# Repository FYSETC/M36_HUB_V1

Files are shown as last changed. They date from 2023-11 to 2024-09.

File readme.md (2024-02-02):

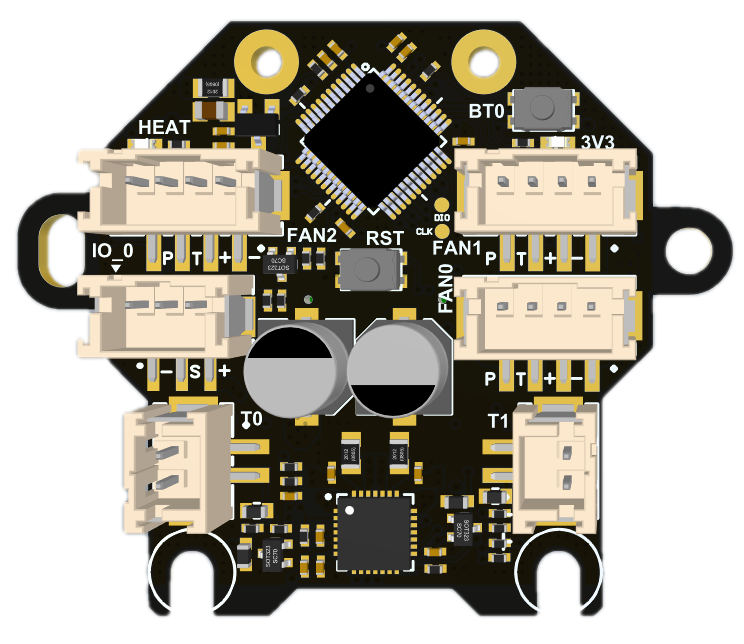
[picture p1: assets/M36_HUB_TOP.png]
M36_HUB_TOP


## 1. Introduction

M36集线板是专门为使用36圆形步进电机（Nema14）而设计的，可以用在mini Stealthburner 或者其他使用36电机的打印头上。该板可以配合多种主板使用，尤其是我们的catalyst和BullAnt。配合专用连接线材也可适配任何其他使用klipper的系统。

M36分为两个版本，主要是电机驱动芯片不一样，普通版本为TMC2209，与Catalyst主板配合使用；Lite版本为GC6609，与BullAnt主板配合使用。

The M36 hub board is specially designed for use with 36 circular stepper motors (Nema14) and can be used on mini Stealthburner or other print heads using 36 motors. This board can be used with a variety of motherboards, especially our catalyst and BullAnt. With special connection cables, it can also be adapted to any other system using klipper.

M36 is divided into two versions, mainly because of the difference in motor driver chips. The normal version is TMC2209, used with Catalyst motherboard; the Lite version is GC6609, used with BullAnt motherboard.

### 1.1 Feature

- Based on STM32F072
- USB interface or CAN（need addon board）
- Onboard TMC2209 / GC6609 (Lite Version)
- 3 x 4Pin(2pin/3pin compatible) controlled Fans (default VIN power supply, 5V optional)
- 1x signal input / output interface (default 5V power supply, VIN optional , with level shift)
- 2x signal input and output interface (3.3V power supply, with 10K pull-up resistor,without level shift)
- 2X 5V single wire RGB interface (1A MAX)
- 1x 3A MAX PWM output for heating rod
- 2x ADC interface for heating temperature or other needs
- 1x onboard thermistor for board temperature or champer temperature monitor
- Comes with 250mm 4-core cable
- 24V/7A max Power Supply
- Comes with terminal housing and wire crimping tabs
- Onboard ADXL345

## 2. Hardware Guide

### 2.1 Install

5. 

### 2.2 Connectors

| Connector name | Type | Details |
| --- | --- | --- |
| IO_0 | PH2.0-3P | PB5，for input and output, with level shift,  hardware pull-up 10k resistor to 3.3v with 100R series resistor. <br><br/>Use For:  <br>Proximity switch (need 24V )<br/>mechanical switch<br/>Photoelectric switch<br/>24V 4pin fan (TCAH pin is suspended) |
| IO_12 | SH1.0-6P | 1=PB6，2=PB7, for input and output, hardware pull-up 10k resistor to 3.3v with 100R series resistor. <br><br/>Use For:  <br/>mechanical switch<br/>Photoelectric switch<br/>Any digital ouput |
| MOTOR | PH2.0-4P | TMC2209 / GC6609<br>EN : PB1<br>DIR : PB14<br>STEP : PB15<br>DIAG : PA8<br>UART : PA9 |
| INPUT | 0.5mm 2x16 BTB connector | Max 24v 7A input, CAN_TX/USBPM=PA12, CAN_RX/USBDM=PA11 |
| T0 | PH2.0-2P | PA0，ADC，4.7K pull-up to 3.3V |
| T1 | PH2.0-2P | PA3，ADC，4.7K pull-up to 3.3V |
| TB | no connector | PA2，ADC，4.7K pull-up to 3.3V, onboard 100K /3950 thermistor |
| HEAT | XH2.54-2P | PA8，MAX 3A，PWM output，max power recommended: 24V/70W |
| FAN0 | PH2.0-2P | Enable: PB11, (4pin fan = enable, 2pin/3pin fan = PWM control pin)<br/>TACH: PB12, <br/>PWM: PB10, (only for 4pin fan)<br/>0.5A MAX PWM，for fan control (default VIN，5V selectable) |
| FAN1 | PH2.0-4P | Enable: PB4, (4pin fan = enable, 2pin/3pin fan = PWM control pin)<br/>TACH: PB3, <br/>PWM: PA15, (only for 4pin fan)<br/>0.5A MAX PWM，for fan control (default VIN，5V selectable) |
| FAN2 | PH2.0-4P | Enable: PB9, (4pin fan = enable, 2pin/3pin fan = PWM control pin)<br/>TACH: PA10, <br/>PWM: PB8, (only for 4pin fan)<br/>0.5A MAX PWM，for fan control (default VIN，5V selectable) |
| RGB1 | SH1.0-3P | PB13，1A MAX sigal line RGB port, 5V，for NeoPixel, WS2812 |
| RGB2 | SH1.0-3P | PB0, 1A MAX sigal line RGB port, 5V，for NeoPixel, WS2812<br/>安装R39=0-100R，可以将RGB1和RGB2串联起来，仅用PB13控制。<br/>Install R39=0-100R, you can connect RGB1 and RGB2 in series and only use PB13 to control them. |

### 2.3 Wiring

2.3.1 With Bullant

2.3.2 With Catalyst V1

2.3.3  With Catalyst V2

2.3.4 With Spider and Raspberry Pi

### 2.4 SCH DXF STEP

Get SCH, DXF, STEP files on github:

## 3. Firmware Guide

This is only Klipper firmware support. If you are Klipper beginner please check the Klipper firmware build here:  [Installation - Klipper documentation](https://www.klipper3d.org/Installation.html#installation)

### 3.1 Firmware Update

1. Turn on the power of the machine and wait for CM68 to start completely, which will take approximately 30-90s.

2. Press and hold the BT0 button on the M6 without releasing it. Press and hold the RST button for more than 2 seconds and release it. Wait for 3 seconds and release the BT0 button;

3. Enter "lsusb" in the SSH interface and you should see the DFU device appear;

4. "cd klipper" enters the klipper directory

5. "make menuconfig" configure the firmware, as shown below:

  M36_menuconfig

6. "make flash FLASH_DEVICE=0483:df11" to compile and upload;

7. When you see the word "successfully", it means the programming is successful.

1. 打开机器电源，等待CM68完全启动，大致需要30-90s。
2. 按住M6上的BT0按钮不松开，按住RST按键2秒以上松开，等待3S，松开BT0按钮；
3. 在SSH界面输入 ‘lsusb‘ 你应该能看到 DFU 设备出现；
4. ‘cd klipper ’进入klipper目录
5. ‘make menuconfig’ 进行固件配置，如下图：
6. make flash FLASH_DEVICE=0483:df11 进行编译并烧录；
7. 当看到successfully字样的时候表示烧录成功。

### 3.2 Config

 We put the Klipper configuration file in github,  you need to get the DEVICE ID by "ls /dev/serial/by-id", then replace the id in the config file.

On Catalyst and Bull Ant motherboards, the USB path is used by default for connection, and an ID is no longer required. In theory, it can be used after updating the firmware and restarting.

我们将Klipper的配置文件放在github中，需要通过“ls /dev/serial/by-id”获取DEVICE ID，然后替换配置文件中的id。

在催化剂和公牛蚁主板上，默认使用USB路径来进行连接，不再需要ID。理论上，更新完固件，重启之后既可使用。

## Buy

[Taobao](https://item.taobao.com/item.htm?spm=a1z10.3-c.w4002-23828897339.22.229c1613tHAtLW&id=690431280049)

[Aliexpress](https://www.aliexpress.com/item/1005004880078163.html)

[Official website](https://www.fysetc.com/products/fysetc-sb-can-tool-board-based-on-stm32f072-support-klipper-with-tmc2209-axl345-acceleration-sensor-for-3d-printer-parts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)

## Contacts

QQ: 1041794121

Facebook grounp：https://www.facebook.com/groups/197476557529090

Discord：https://discord.gg/Fb6FdND4

email：support@fysetc.com

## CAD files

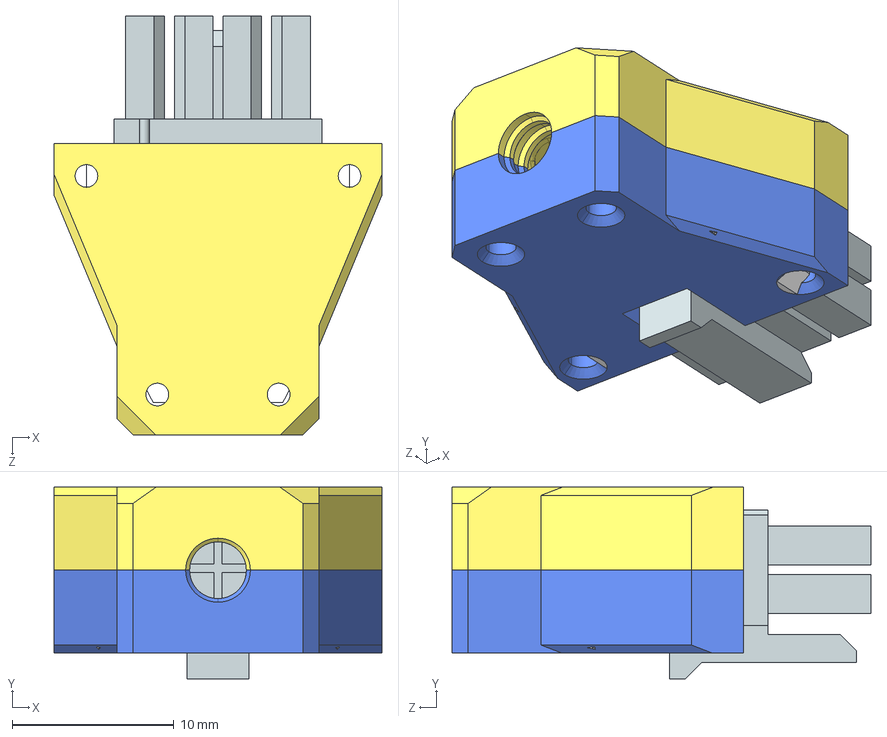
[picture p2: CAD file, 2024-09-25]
hardware/MX3.0-8P-CASE.STEP
20.3 x 11.8 x 25.9 mm
430250810_默认
Part2_默认
Part3_默认
Part4_默认

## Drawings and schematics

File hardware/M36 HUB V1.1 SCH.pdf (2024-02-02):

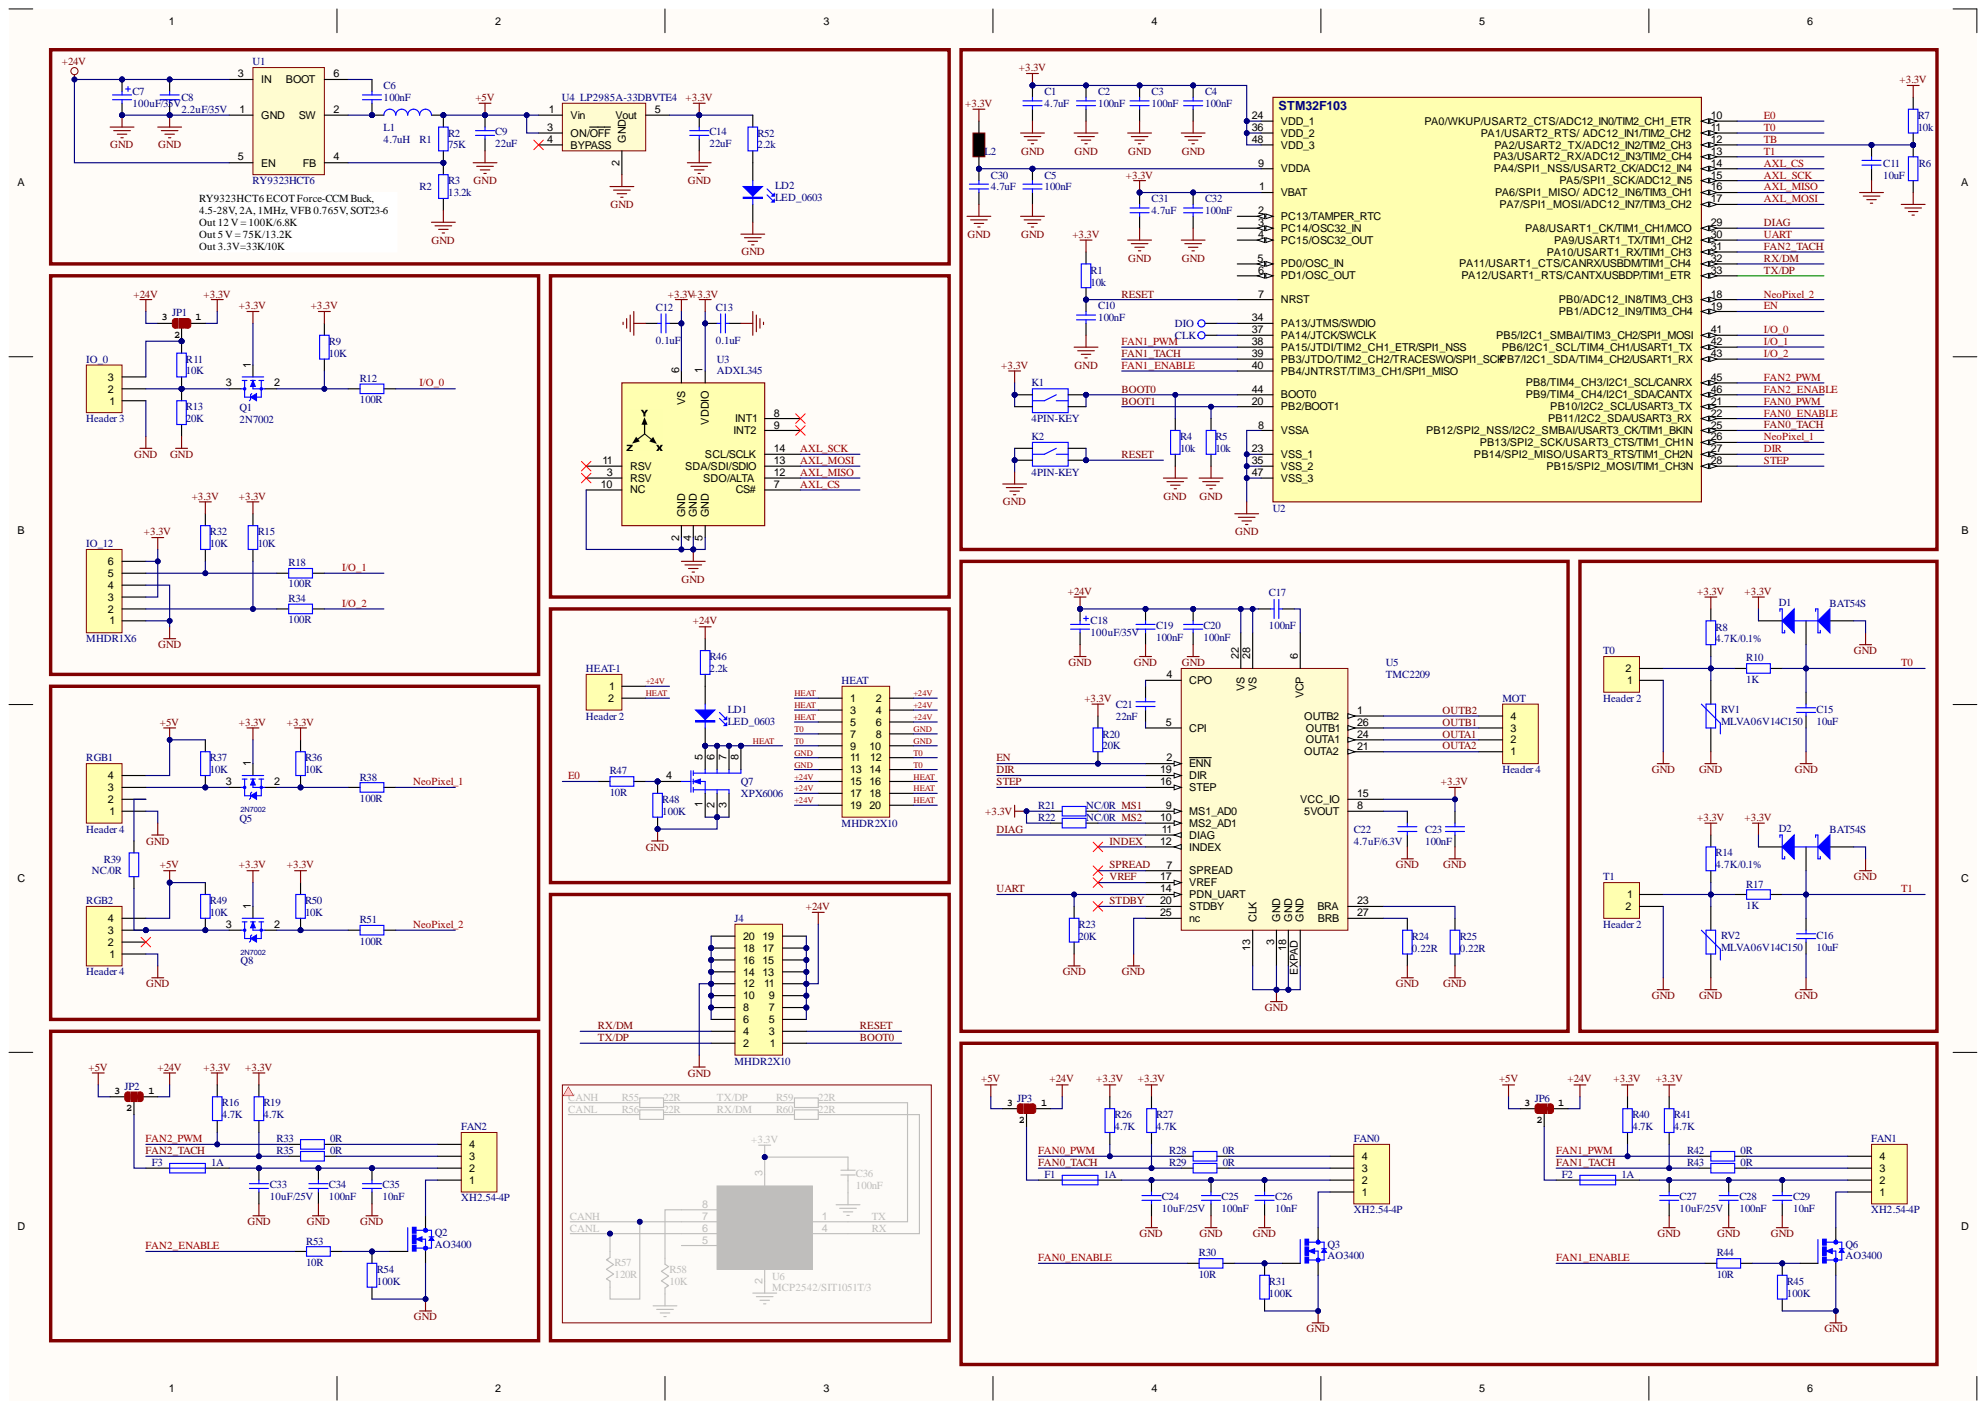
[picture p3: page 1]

C8 | GND 1

ON/OFF 3

VDD_2 36 | T0

VDDA 9 | T1

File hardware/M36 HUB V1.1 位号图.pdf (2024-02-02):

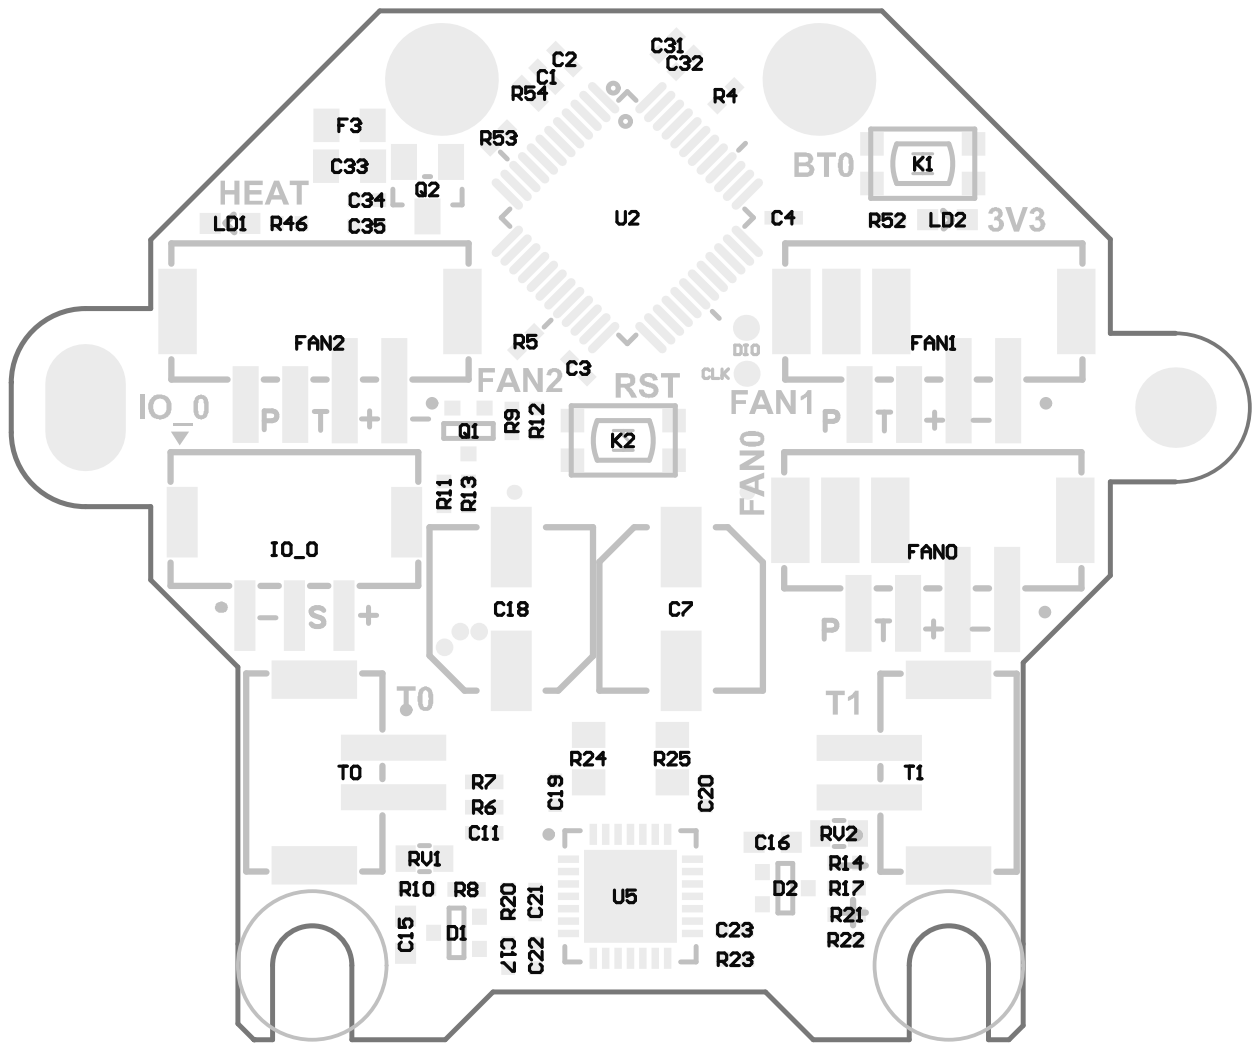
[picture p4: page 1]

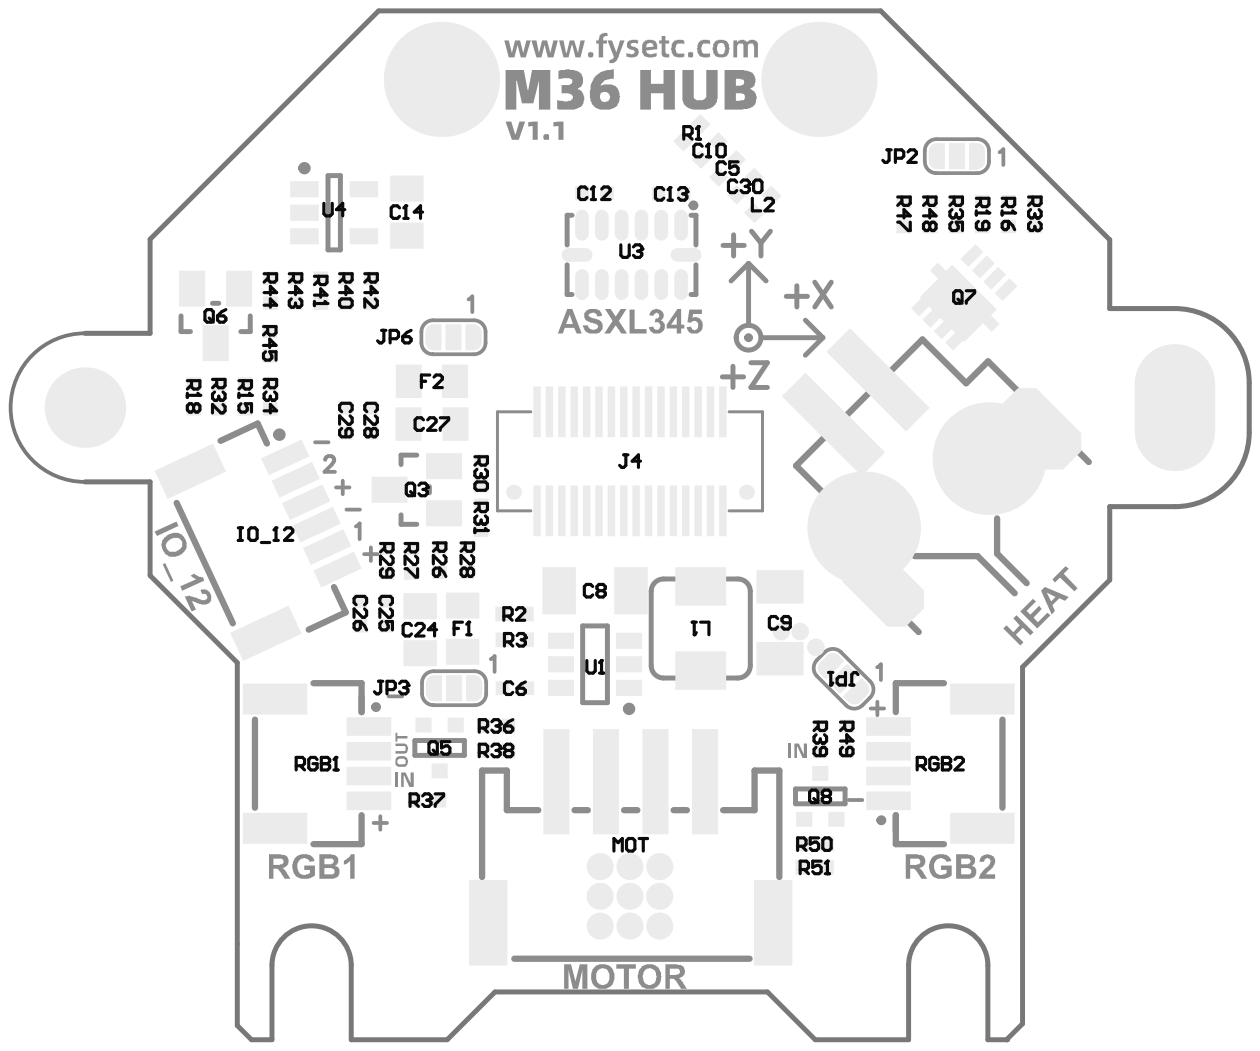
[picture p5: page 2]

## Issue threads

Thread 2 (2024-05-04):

Need Klipper config for this

zachdev, 2024-05-04:
Where is the klipper head.cfg that is required for this?

danyial, 2024-05-13:
Need it too

cdiesch, 2024-06-03:
I also need the head.cfg. My machine shipped with a dead cm68 and the replacement one does not have the correct config files.

mayder, 2024-06-19:
Need it too, because I want configure the ADXL345

kkobold, 2024-07-16:
need it too

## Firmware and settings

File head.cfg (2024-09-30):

## M36 HUB V1.1 Lite （with GC6609）
## For more info 
## https://github.com/FYSETC/M36_HUB_V1
## https://wiki.fysetc.com/M36_HUB_V1/

# This file contains common pin mappings for the Fysetc M36 HUB V1.1
# To use this config, the firmware should be compiled for the
# STM32F072 with "No bootloader" ,"Internal clock" and Communication interface USB

# How to get in DFU mode:
# 1. hold BT0 button for 2 seconds
# 2. Hold RST button for 2 seconds
# 3. Release the BT0 button
# 4. wait 2seconds
# 5. Release the RST button
# "lsusb" check if get in DFU mode

# After running "make", run the following command to flash the board:
# "dfu-util -R -a 0 -s 0x08000000:leave -D out/klipper.bin" to upload
# or "make flash FLASH_DEVICE=0483:df11" compile and upload at once.


## *** THINGS TO CHANGE/CHECK: ***
## MCU path                                                                     [mcu] section
## Z and Extruder motor currents                                                [tmc2208 stepper_*] sections. Uncomment the stepper motor you have
## Full steps per rotation for Extruder                                         [extruder] section
## Thermistor types                                                             [extruder] and [heater_bed] sections - See https://www.klipper3d.org/Config_Reference.html#common-thermistors for common thermistor types
## Extruder motor currents                                                      [extruder] section
## PID tune                                                                     [extruder] and [heater_bed] sections
## Fine tune E steps                                                            [extruder] section

## For more info                                                                check https://docs.vorondesign.com/build/startup/#v0
## See docs/Config_Reference.md for a description of parameters.

[mcu head]
serial: /dev/serial/by-path/platform-4101000.usb-usb-0:1.4:1.0
#restart_method: command


#####################################################################
#   Extruder
#####################################################################

[extruder]
step_pin: head:PB15
dir_pin: head:PB14	                # Add ! if moving opposite direction
enable_pin: !head:PB1
full_steps_per_rotation: 200    # Set to 200 for 1.8 degree motor, set to 400 for 0.9 degree stepper motor
rotation_distance: 22.23        # See calibrating rotation_distance on extruders doc
gear_ratio: 50:10               # For Mini Afterburner
microsteps: 32
nozzle_diameter: 0.400
filament_diameter: 1.750
heater_pin: head:PA0
## Check what thermistor type you have. See https://www.klipper3d.org/Config_Reference.html#common-thermistors for common thermistor types.
## Use "Generic 3950" for NTC 100k 3950 thermistors
sensor_type: Generic 3950
sensor_pin: head:PA1
control: pid            # Do PID calibration
pid_Kp: 28.182
pid_Ki: 1.978
pid_Kd: 100.397
min_temp: 0
max_temp: 270
min_extrude_temp: 10  # set 10 to test,please change to 170 for real use
max_extrude_only_distance: 150
max_extrude_cross_section: 1.5
pressure_advance: 0.2   # See tuning pressure advance doc
pressure_advance_smooth_time: 0.040

[tmc2209 extruder]
uart_pin: head:PA9
interpolate: False
run_current: 0.7
diag_pin: head:PA8   
sense_resistor: 0.220
stealthchop_threshold: 0                                            # Set to 0 for spreadcycle, avoid using stealthchop on extruder


#####################################################################
# Fan Control
#####################################################################
#FAN0_EN:PB11
#FAN0_PWM:PB10
#FAN0_TACH:PB12

#FAN1_EN:PB4
#FAN1_PWM:PA15
#FAN1_TACH:PB3

#FAN2_EN:PB9
#FAN2_PWM:PB8
#FAN2_TACH:PA10

[heater_fan hotend_fan]
pin:head:PB4
max_power:1.0
shutdown_speed:0.0
cycle_time:0.5
hardware_pwm:false
kick_start_time:0.10
off_below:0.1
#tachometer_pin:
#tachometer_ppr:
#tachometer_poll_interval:
#enable_pin:
heater: extruder
heater_temp: 50.0
fan_speed: 1.0

[multi_pin part_cooling]
pins: head:PB9,head:PB11

[fan]
pin: multi_pin:part_cooling

#####################################################################
# Temperature Sensor
#####################################################################

[temperature_sensor head_mcu_temp]
sensor_type: temperature_mcu
sensor_mcu: head
min_temp: 0
max_temp: 100

[temperature_sensor Chamber_on_M36]
sensor_type: EPCOS 100K B57560G104F
sensor_pin: head:PA2
min_temp: 0
max_temp: 100

#####################################################################
# Neopixel
#####################################################################

[neopixel left_rgb]     
pin: head:PB13
chain_count: 1
color_order: GRB
initial_RED: 0.1
initial_GREEN: 0.1
initial_BLUE: 0.1

[neopixel right_rgb]
pin: head:PB0
chain_count: 1
color_order: GRB
initial_RED: 0.1
initial_GREEN: 0.1
initial_BLUE: 0.1

# If you want the LEDs on both sides to be synchronized, you can also use multi_pin to configure it.
# [multi_pin rgb]
# pins: head:PB0,head:PB13
# [neopixel rgb]
# pin: multi_pin:RGB
# chain_count: 1
# color_order: GRB
# initial_RED: 0.9
# initial_GREEN: 0.9
# initial_BLUE: 0.9

#####################################################################
#   ADXL345
#####################################################################

[adxl345]
cs_pin: head:PA4
#   The SPI enable pin for the sensor. This parameter must be provided.
#spi_speed: 5000000
#   The SPI speed (in hz) to use when communicating with the chip.
#   The default is 5000000.
spi_bus: spi1
#spi_software_sclk_pin:PA5
#spi_software_mosi_pin:PA7
#spi_software_miso_pin:PA6
#   See the "common SPI settings" section for a description of the
#   above parameters.
axes_map: -x, z, y
#   The accelerometer axis for each of the printer's X, Y, and Z axes.
#   This may be useful if the accelerometer is mounted in an
#   orientation that does not match the printer orientation. For
#   example, one could set this to "y, x, z" to swap the X and Y axes.
#   It is also possible to negate an axis if the accelerometer
#   direction is reversed (eg, "x, z, -y"). The default is "x, y, z".
rate: 3200
#   Output data rate for ADXL345. ADXL345 supports the following data
#   rates: 3200, 1600, 800, 400, 200, 100, 50, and 25. Note that it is
#   not recommended to change this rate from the default 3200, and
#   rates below 800 will considerably affect the quality of resonance
#   measurements.

[resonance_tester]
accel_chip: adxl345
accel_per_hz: 75  # default is 75
probe_points:
    60, 60, 20  # an example

[input_shaper]
shaper_freq_x: 66
shaper_type_x: ei
shaper_freq_y: 70.8
shaper_type_y: mzv

[menu __main __octoprint]
type: disabled
